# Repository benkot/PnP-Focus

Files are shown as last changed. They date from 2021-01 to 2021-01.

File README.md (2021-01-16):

This is a fork of the PnP-Focus project started by Anat available here:

https://github.com/aruangra/PnP-Focus

Since there are significant Changes with this V2.0 version compared to the original project, let's start fresh with the features.

# PnP-Focus Version 2.0

## Objective:
To build a focus controller which takes arduino controller boards and plug-in controller shields to assemble a focus controller with minimal soldering or wiring.

## Two versions of the project:
* Standalone PNP-Focus Controller
* PnP-Focus Stick Controller

## Features:
* Manual control.
* LCD display (Optional)
* Temperature sensor.
* Local manual motor control using automatic increasing speed changes.
* Independent motor speeds for local button focus position and ASCOM commanded position
* Stepper motor output power down after a positional move to prevent motor from heating due to quiescent current.
* Ability to drive Uni-Polar or Bi-Polar stepper motors.
* Full step and half step motor movements.  
* Switching between full step and half step automatically converts the position counter to new step count and correct transition step code.
* Ability to save position and step mode to non-volatile memory and recall on power-up to restore unit to previously used configuration

* Compatible with Moonlite DRO ASCOM driver with the following compatibility features:
    * Full selection and operation of moonlight DRO ASCOM step speeds using 16, 32, 64, 125, 250 steps/second.
    * Temperature sensor for temperature compensation by ASCOM driver.  Temperature sensor moved to pin A2.
    * ASCOM connection locks mode to driver selected Full step or Half step  mode.
    * ASCOM stop or disconnect records stepper position and step mode to non-volatile memory.

* Additional features added when operating in ASCOM connection which are not provided by    Moonlite Technologies DRO driver:
    * Backlash compensation for outward movement to compensate for gravity and to ensure consistent approach to focus position in either direction.
    * ASCOM moves use soft start with speeds increasing at driver speed intervals, up to the selected driver step speed setting.
    * ASCOM move command have reducing speed as target position is approached to to ensure positional accuracy and repeatability.
    * Provides the ability to use high speed focus slews without loss of accuracy or repeatability.
* Compatible with commercially available focus drives using stepper motors
* Works with the popular stepper motors:
    * ABS3008-002  (12V) RoboFocus Stepper Motor
    * LSG35012F76P (12V) Moonlite Telescope Hi-Resolution Stepper Motor
    * 28BYJ-48  (5V and 12V)
    * 17HS13-0404S-PG27 (12V)

## Installation:

The Original Installation upload approach is obsolete and not use with this version.  Requires users to use the Arduino Integrated Development Interface (IDE) program to load the Arduino firmware files.  The use must modify the user configuration header area to match the code to their specific build and then compile and upload the file to the arduino.  All the individual files are available 
https://github.com/benkot/PnP-Focus 

The entire project files are availble in a zip download in the Github folder to make it easier to prepare and install the firmware.

## Documentation:
Project manual describing the necessary hardware, installation, assembly, user controls and operating principles is available in the Github folder

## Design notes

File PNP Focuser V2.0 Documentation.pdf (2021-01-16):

# Plug N Play

# Focus Controllers

V2.0.2

compiled by Todd Benko, 2021

## Table of Contents

## PREFACE

## Disclaimer

This project is released into the public domain as is where is, with no obligation or responsibility accepted on the part of the author, for any mishaps or failures caused by this product or use of this product. Users intending to use this project or code do so at their own risk and usage of product and code is deemed to be acceptance of those risks. The author(s) accept no responsibility to damage caused to any equipment or goods or self by using the ideas, schematics and code associated with this project, or loss of income or all other losses that may be incurred. No warranty is offered or implied.

## Copyright Restrictions

The schematic, firmware and other code and ideas are released into the public domain. Users are free to implement these for their personal use, but may NOT sell projects based on (or derived from) this project for commercial gain without express written permission granted from the author(s).

## Firmware License Restrictions

If you copy or write new code based on the code in these files you must include a link to these files AND you must include references to the author(s) of this code. Firmware is released subject to the following restrictions

© Copyright Orly Andico, 2014
© Copyright Anat Ruangrassamee, 2017
© Copyright Michael Fulbright, 2018
© Copyright Todd Benko, 2020

Permission is hereby granted, free of charge, to any person obtaining a copy of this software and associated documentation files (the "Software"), the rights to use, copy, modify, merge, publish, distribute, sublicense copies of the Software (from the authors), subject to the following conditions:

1. The above copyright notice shall be included in all copies or substantial portions of this Software.
2. The software may NOT be sold or charged for in any way, either as part of a package, license fee, annual charges or premiums and shall include the copyright notice above.
3. The source-code to any software MUST be made available in full source-code form (including modified source files) and free to download without payment and include the copyright notice above

THE SOFTWARE IS PROVIDED "AS IS", WITHOUT WARRANTY OF ANY KIND, EXPRESS OR IMPLIED, INCLUDING BUT NOT LIMITED TO THE WARRANTIES OF MERCHANTABILITY, FITNESS FOR A PARTICULAR PURPOSE AND NONINFRINGEMENT. IN NO EVENT SHALL THE AUTHORS OR COPYRIGHT HOLDERS BE LIABLE FOR ANY CLAIM, DAMAGES OR OTHER LIABILITY, WHETHER IN AN ACTION OF CONTRACT, TORT OR OTHERWISE, ARISING FROM, OUT OF OR IN CONNECTION WITH THE SOFTWARE OR THE USE OR OTHER DEALINGS IN THE SOFTWARE.

## INTRODUCTION

## Overview

An Arduino-based focus controller named "PNP-Focus". As the name implies, it is to be as easy as "Plug and Play" with little or no soldering. No hassle with firmware upload.
You simply 1) buy the readily available components, 2) stack them, and 3) upload the firmware. The PNP-Focus is just the controller. You still need to mount a stepper motor on your telescope connected to this controller. With motorized focuser you get the higher resolution since a stepper motor may have 2000-6000 steps per revolution. The higher resolution is crucial for imaging. You have the option to control the focuser locally or remotely from the Personal computer (PC). When you do imaging, you control your devices via a PC and software. PC based then leads to automated focusing.

## Features in V2

- Manual control.
- LCD display (Optional)
- Temperature sensor.
- Local manual motor control using automatic increasing speed changes.
- Independent motor speeds for local button focus position and ASCOM commanded position
- Stepper motor output power down after a positional move to prevent motor from heating due to quiescent current.
- Ability to drive Uni-Polar or Bi-Polar stepper motors.
- Full step and half step motor movements.
- Switching between full step and half step automatically converts the position counter to new step count and correct transition step code.
- Ability to save position and step mode to non-volatile memory and recall on power-up to restore unit to previously used configuration
- Compatible with Moonlite DRO ASCOM driver with the following compatibility features:
- Full selection and operation of moonlight DRO ASCOM step speeds using 16, 32, 64, 125, 250 steps/second.
- Temperature sensor for temperature compensation by ASCOM driver. Temperature sensor moved to pin A2.
- ASCOM connection locks mode to driver selected Full step or Half step mode.
- ASCOM stop or disconnect records stepper position and step mode to non-volatile memory.
- Additional features added when operating in ASCOM connection which are not provided by Moonlite Technologies DRO driver:
- Backlash compensation for outward movement to compensate for gravity and to ensure consistent approach to focus position in either direction.

- ASCOM moves use soft start with speeds increasing up to the selected driver step speed setting.
- ASCOM move command have reducing speed as target position is approached to to ensure positional accuracy and repeatability.
- Compatible with commercially available focus drives using stepper motors
- Works with the popular stepper motors:
- ABS3008-002 (12V) RoboFocus Stepper Motor
- LSG35012F76P (12V) Moonlite Telescope Hi-Resolution Stepper Motor
- 28BYJ-48 (5V and 12V)
- 17HS13-0404S-PG27 (12V)

Exceptions
- PNP-Focus units will not drive DC or AC servo motors used in some focuser drive systems.

Caveat
The goal behind PNP-Focus was to use off the shelf components, plug them together without the need to perform any soldering. The primary components can be assembled within the design scope. The real issue could be the components you select to assemble your project may indeed require some assembly or soldering activities. Many of the components from suppliers may in fact not have the header wires installed. Also depending on your housing your interface connections may requires some assembly or soldering. Interface components such as power wires, motor connectors may require soldering assembly depending on components that you source.

## Hardware Variations

There exist two design hardware versions. Both version offer computer focus control through the Moonlight DRO Ascom driver. There is the full size

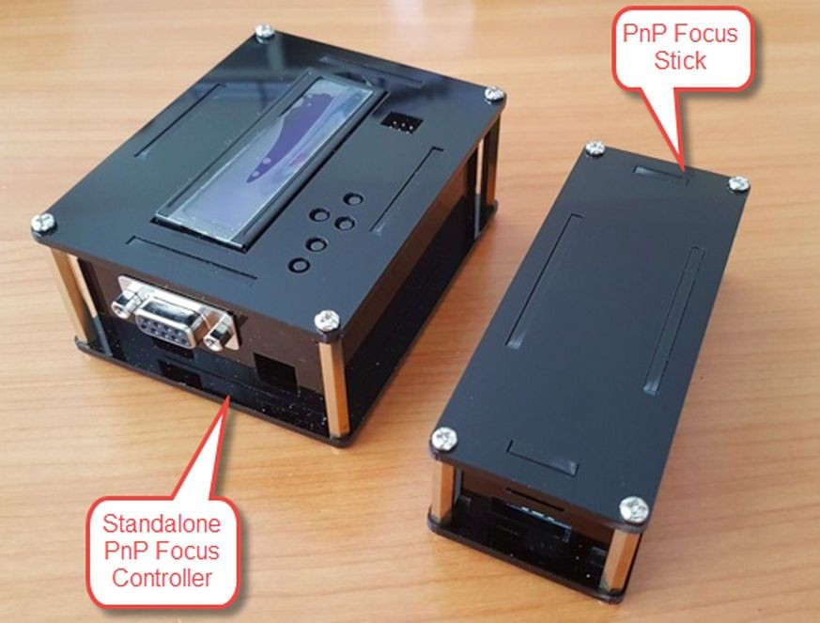
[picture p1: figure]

standalone PNP-Focus Controller offers USB and local button focus control. The PNP-Focus Stick only provides computer focus control via the USB port.

Standalone PNP-Focus Controller
The Standalone focus controller is intended to provide a user with direct control of the focus motor without any need for software or computer. The designed is based on the Arduino Leonardo board, using a plug in LCD1602 display shield as the user interface. The display shield offers a 2 line x 16 character display for status information. The shield includes 6 tactile buttons to provide manual focuser control without any computer connection. Telescopes with an electronic focuser can be used without the need to connect to any computers nor the need to remove the focus motor for simple astronomy usage.
The standalone focus control still provides full computer control when connected using the arduino USB connection and the moonlite DRO ASCOM driver. The same design can run headless, without the LCD1602 display shield installed. The variation would provide using only computer control in the similar form factor.

Required Components

1) Arduino Leonardo ATMega32U4 Controller
The Leonardo board with the ATMega32U4 chip is the board that was used for this build. Technically the pin layout for the Arduino and the Ardumoto board would line up for use with other Arduino controller boards. For simplicity sake just use the Arduiono Leonardo. The code may work with other Arduino board with the same footprint because you use the Arduino integrated development environment (IDE) program to load the firmware. We leave that choice up to those who want to play rather than just using what was chosen for the PNP focus platform.
search “Arduino Leonardo” on by Arduino or keyestudio on Ebay, Amazon or Aliexpress Keyestudio Leonardo, (https://www.aliexpress.com/store/product/Free-shipping-leonardo-R3-development-board-USB-Cable-compatible-for-arduino/1452162_32310214921.html) Ebay, (https://www.ebay.com/b/arduino-leonardo/bn_7024816151)
2) Ardumoto L298P Motor Drive Board
Ardumoto L298P motor drive board can be purchased with different pin assignments The standard for this programs uses

D3 -A motor PWM drive
D11-B motor PWM Drive
D12-A Dir
D13-B Dir
The L298P board is capable of driving up to 2A current per motor connection.
To make things easy just ensure the board you purchase uses Pin 3, 11, 12, 13

for driving the motor. Fortunately, most of them are. Also ensure the socket with leads come with kit so stacking above and below board is available. Search “ardumoto L298P on Ebay, Amazon or AliExpress. Do not confuse this with Ardumoto version 2.3 boards using L293D chips. Their control is totally different and not compatible.

Many of the ardumoto boards come with surface mount pad instead of jumper
pins to select the logic voltage between 5Volts and 3.3Volts. The Leonardo
requires using 5 Volt logic to be selected. Ensure that you place a solder

bridge on the 5V selection pads to set the correct logic voltage. A small single
strand of wire helps to make this bridge. Make sure there is no connection to the
3.3V pad. If it is not selected, move commands will just cause the stepper to vibrate or move really slowly when issuing a move command. This issue was most people’s problem in building their PNP-Focus controller.

Keyestudio Ardumoto Shield (https://www.aliexpress.com/store/product/Free-shipping-L298p-Motor-shield-motor-drive-for-arduino/1452162_2043390148.html) , Ebay (https://www.ebay.ca/sch/i.html?_from=R40&_trksid=p2380057.m570.l1313&_nkw=ardumoto+shield&_sacat=0)

3) 1602 LCD and Keypad Shield
Search “1602 LCD and keypad shield” on DFRobot, Ebay, Amazon. There are various 1602 keyboard shields available and most should work. LCD shield for this project uses Pins D4-D10 and A0. The differences are usually button sizes, additional interface pin and how the LCD
contrast is adjusted.
1602 Shield for this project uses the following pin assignments
D4-LCD D4
D5-LCD D5
D6-LCD D6
D7-LCD D7
D8-LCD Reset
D9-LCD Enable
D10-LCD BackLight brightness adjustment
A0 – is button decoding.

Button readings have two different analog ranges depending on which version is purchased. Need to select using comments // which pin assignment works for your LCD shield in read_LCD_buttons() function.

Make sure the one you select works for the case you plan to use and how you plan to implement the temperature sensor. The DFRobot has longer tactile button caps and has pins to make temperature sensor connection to the LCD shield through the top of the case using solderless pin connections. Others have lower tacktile buttons and there is no need for any pins on top surface so you want pins on the bottom for stacking onto the ardumoto shield. If you do not want to make a different temperature connection through the LCD top surface, use the breakout area of the ardumoto to wire in your temperature sensor connections using soldered wire connections. You could use an internal temperature sensor, an external one through the motor drive cable or a seperate standalone plugin that uses a headphone jack connection which could disconnect an internal temperature sensor connection.

Keyestudion LCD1602 Shield (https://www.aliexpress.com/store/product/1602LCD-Keypad-Shield-For-Arduino-LCD-Display-ATMEGA328-ATMEGA2560-For-Raspberry-Pi-UNO-Blue-Screen-Blacklight/145216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) , Amazon (https://www.amazon.ca/Keypad-Shield-Backlight-arduino-Robot/dp/B07F7GCZNV?s=electronics) , Ebay, (https://www.ebay.ca/sch/i.html?_nkw=Lcd%201602%20Keypad%20Shield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) AliExpress (https://www.aliexpress.com/premium/keypad-shield-lcd1602.html?d=y)

4) DS18B20 Temperature Sensor and Interface
There are so many different ways to connect the DS18B20 temperature Sensor. For the PNP-Focus the sensor data pin will connect to the Analog A2 Arduino pin. The original PNP-Focus used pin A2, however the PNP-Focus stick has a conflict with nano-motorshield. Therefore this version
and firmware code is looking for temperature probe data on Analog pin A2.

The interface requires that the data pin be pulled up to 5V with a pull up resistor either by a non-soldered interface board or by your own wiring application. It basically
depends on your assembly comfort level. The temperature sensor is only

used for temperature compensation focus position moves. The temperature
must reflect the temperature change of your telescope and it will vary unit design variances. There are assembled boards which have resistor and indicator diodes already installed that might be able to placed on outside of housing and just require running wires to the Arduino pins.
Another approach would use a waterproof external temperature probe which would be attached to the shell of the telescope to measure the temperature changes. Another approach might be to install the temperature sensor or module board in the dB9 connector which attaches to the focuser motor. All approaches
may have their differences and any application of temperature compensation is
based on an observed response based on either temperature sensor location.

Using either method you need to observe the focus changes which occur with your telescope prior to applying a temperature compensate rate.
The moonlite focuser lists commands as though temperature compensation would be applied by the focus controller. Moonlight Telescopes Ltd has been determined that temperature compensation is better managed by the ascom driver, rather than the hardware
interface. It has been validated that the temperature
compensation commands listed in the hardware command
interface are not issued by the driver when temperature

compensation is selected. As a result temperature compensation is not enabled when operating the as a standalone controller. The fact that manual focus control is more important to adapt to different users in visual astronomy or other standalone astronomy usage rather than the benefits offered by temperature compensation.

Keyestudio DS18B20 (https://www.aliexpress.com/item/32884815508.html?spm=2114.12010612.8148356.3.6e6f1aeeuFA1dI) , Amazon (https://www.amazon.ca/Waterproof-Temperature-Stainless-Plugable-Terminal/dp/B07LFJR3J7) , AliExpress (https://www.aliexpress.com/item/1834551892.html?src=google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) , Voltateck (https://voltatek.ca/sensors/145-temperature-sensor-ds18b20-module-board.html)

5) Interface Components
You need a variety of interface components to power and connect your PnP Standalone Focus Controller to your focus motor assembly.

Vin Power connection:
12V power cable to power the Arduino and Stepper motor. The ardumoto shield will not drive the stepper motor with only USB power applied. The ardumoto shield requires that Vin
power be supplied at the voltage required to drive the stepper motor. Typically recommend
using 12V stepper motor. The Vin can be connected using the barrel connection of the
Leonardo or the terminal strip on the ardumoto. For the PNP-Focus Stick it must be connected to the terminal strip. Solderless barrel connectors are available from various sources.
Amazon (https://www.amazon.ca/VCE-Pairs-2-1x5-5mm-Adapter-Camera/dp/B078X47M5H) , Adafruit (https://www.adafruit.com/product/368) , Ebay (https://www.ebay.ca/sch/i.html?_nkw=Barrel%20To%20Screw%20Terminal%20Connector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)
- USB micro cable to program the arduino and to drive unit with PC using
ASCOM driver. The assembly of the PNP-Focus does not provide good accessibilty to the USB interface. One solution is to use a USB patch cord with a panel mount usb connector. This way you do not need a specific as built case to house the PNP-Focus controller. To conserve space, recommend looking for
the 90 right or left usb patch cords.
AliExpress (https://www.aliexpress.com/item/32805000569.html)
- A cable interface from the controller to the motor. Many focus motors use a dB9 connection. A dB9 male-female cable would be used if a dB9 connector was installed on the controller housing
- option using an Ethernet cable and installing a female Ethernet jack on the controller housing and then a RJ45-dB9 adapter at the motor drive connection.

Standalone Computer Only Configuration Option
If you like standalone hardware and case you plan to use and only want to drive it from a computer ASCOM driver, you can just omit the installation of the LCD1602 display and keyboard shield to produce only computer access focus control. For this configuration, you need to adjust the user configuration in the arduino firmware code to comment out LCD1602 display and keyboard shield as it is not installed.

Case and Housing Options
Standalone PNP-Focus Controller builders have found various methods to enclose their controller boards. Anat used flat laser cut plexiglass material to create a jointed box which is fastened together with 4 screws. The laser cut dxf files are included in the zipped file assembly.

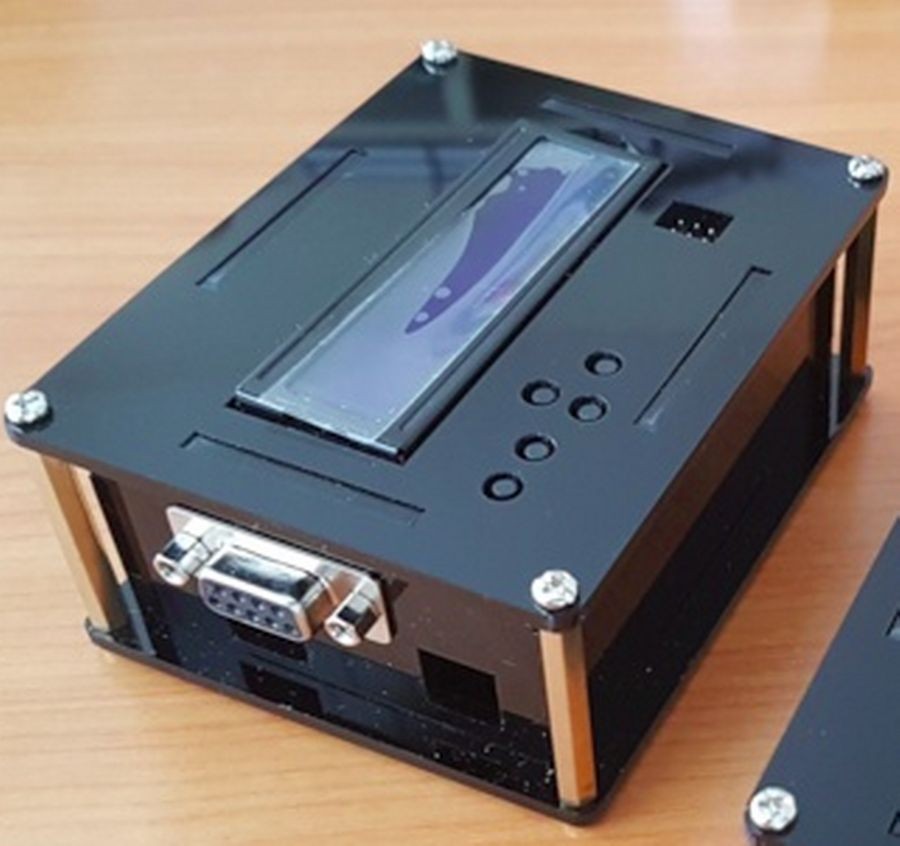
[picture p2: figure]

Mr. Tom K. created a 3D printed case and lid to enclose his standalone PNP-Focus controller.

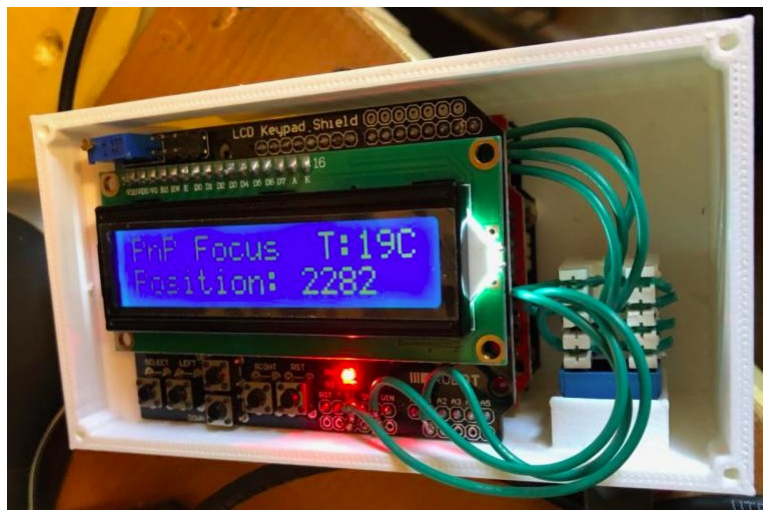
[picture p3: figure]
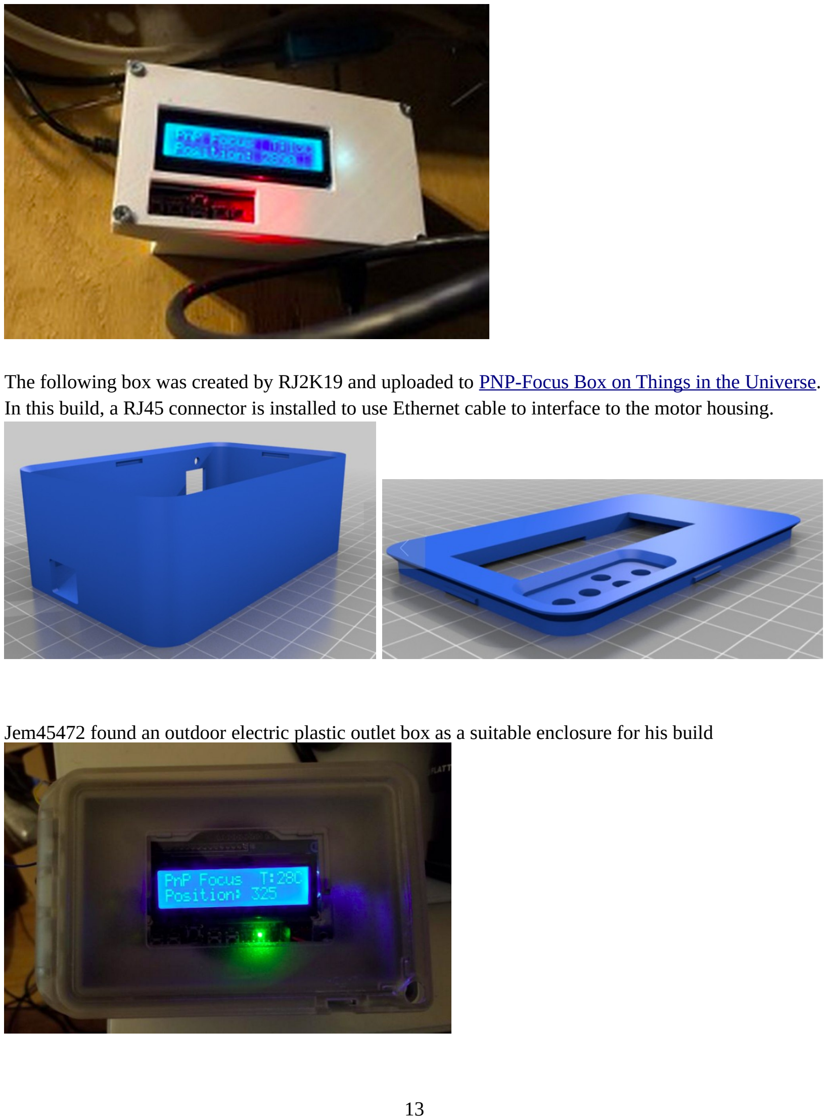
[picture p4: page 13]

The following box was created by RJ2K19 and uploaded to PNP-Focus Box on Things in the Universe. (https://www.thingiverse.com/thing:4075523) In this build, a RJ45 connector is installed to use Ethernet cable to interface to the motor housing.

Jem45472 found an outdoor electric plastic outlet box as a suitable enclosure for his build

I used a standard plastic Hammond case 120mm x 65mm x 40mm and just carved out the holes and slots for the interface components.

Assembly Notes:
1. Many of the Arduino and shields do not come assembled with the stacking pins installed. The ardumoto board is in the middle of the stack so it must have stack-able headers installed.

When you stack the boards together, you want to ensure pins are aligned such that all digital and Analog I/O pins align on each stacked board.

2. Wiring the stepper motor is a bit confusing. It doesn’t help when board silkscreen numbers or user documentation doesn’t match with assembled components. For instance Moonlite hi-res focuser is documented as the following pin and wire colour assignment.

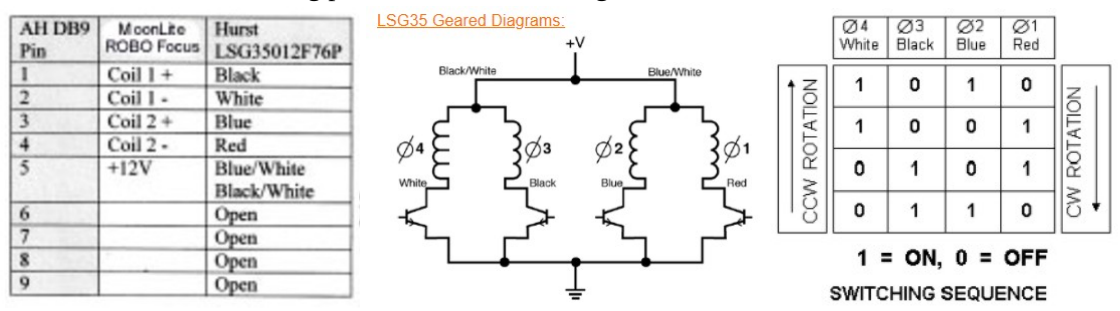
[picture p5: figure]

However, disassembly of a Moonlite hi-res focus motor on a Newt telescope found Blue on the dB9-pin 1, Red on pin 2, Black on pin 3 and white on pin 4 and the blue/White/ Black/White wires both connected to pin 5. This is a significant difference and if we plot out true table in firing the same order but in a different wire order we find the following:

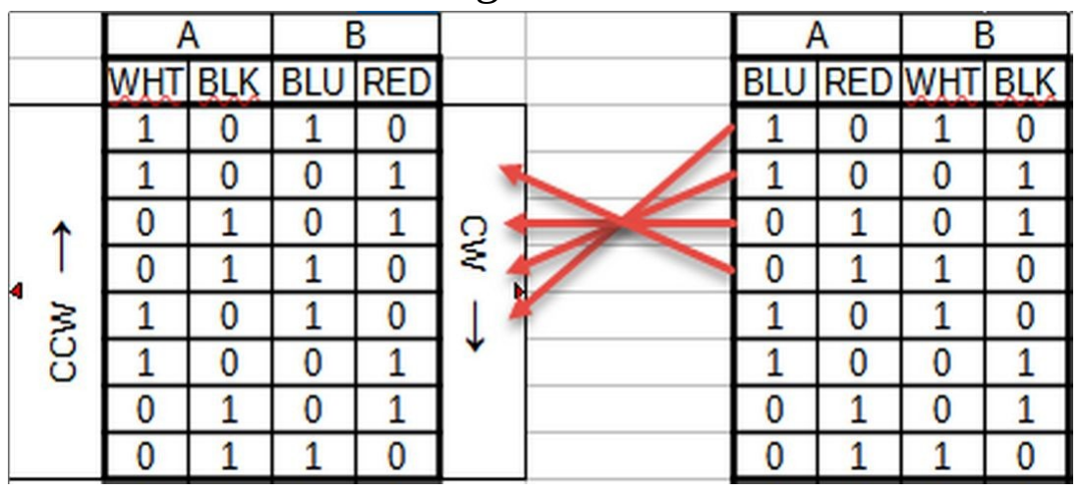
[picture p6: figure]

The left side is the documented order and the right is same order firing but wired in reverse. If we look for the same exact logic sequence of the right table in the left, we find the firing order produces an opposite rotational direction.

This is significant to your installation of
the stepper motor to the telescope. The
focus controller is designed where

increasing the step count produces an outward focus movement. If you find that your motor is running inward with increasing motor steps, all you need to do is swap the wires in pair A and B output on the Motor shield or on your stepper motor connector. Voila, the focus runs in the correct direction. More details about the specific wiring connection are provided later in the Operating Principals section.

## PNP-Focus Stick Controller

The desire to have a smaller focus controller which can only be controlled by computer appeals to many users. With computer access control, there is no need for the display and keyboard shield. You could simply not install the LCD1602 shield and use the stand alone board configuration. However there is a smaller Arduino unit which can make a smaller focus controller unit. The PNP-Focus Stick uses an Arduino MICRO board with a nano motor shield which fits the smaller pin layout configuration.

Components required:

1) Arduino Micro ATmega32u4 Controller:
Ensure you select the Arduino Micro ATmega32u4 5V 16MHZ

100% for Arduino Micro Replace pro mini and not the Mini or Mini Pro versions as those have a different pin footprint which does not match the motor shield. When assembling this board you need to ensure the pins are installed pointing downwards so it will plug into the and above the NANO motor shield.
Ebay, (https://www.ebay.ca/itm/New-Arduino-Micro-ATmega32u4-5V-16MHZ-100-for-Arduino-Mirco-Replace-pro-mini/331809999256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)
2) NANO Motor Shield:
Nano motor shield board is believed to be standardized with the same pin assignments used in the program. When searching, just confirm the following pin assignments.
The standard for this programs uses
D3 -A motor PWM drive
D11-B motor PWM Drive
D12-A Dir
D13-B Dir
To make things easy just ensure the board you purchase uses Pin 3, 11, 12, 13 for driving the motor.
The shield can supply 2 amperes per channel, for a total of 4 amperes
maximum.
Input and Output

This shield has two separate channels, called A and B, that each use 4 of the For Arduino pins to drive or sense the motor. In total there are 8 pins in use on this shield. You can use each channel separately to drive two DC motors or combine them to drive one Bi-Polar stepper motor. PNP-Focus only uses the code to drive the stepper motor operation and not the DC motor operation. The shield's pins, divided by channel are shown in the table below:
Function | pins per Ch. A pins per Ch. B
Direction | D12 | D13
PWM | D3 | D11
Brake | D9 | D8
Current Sensing A0 | A1

AliExpress (https://www.aliexpress.com/item/32799216665.html) , Amazon (https://www.amazon.ca/Nano-L298P-Channel-H-Bridge-Stepper-Driving/dp/B07KFBNSTD) , EBay (https://www.ebay.ca/sch/i.html?_from=R40&_trksid=p2380057.m570.l1313&_nkw=nano+motor+shield&_sacat=0)
3) Temperature: Can use the same resources as the PNP-Focus stanalone version. Soldering or wirewrap required to pins into place for proper temperature placement. For the temperature you need the same connections as in the standalone version to +5V, Ground (GND) and the centre data pin connected to Analog 2 (A2) pin. It is conceivable that the PNP-Focus Stick would be used to build a complete focus assembly with the controller and motor in one housing and attached directly to the telescope. In this situation you really need to ensure the temperature probe gets outside the housing. Both the stepper motor and the Arduino boards will produce heat inside the housing. That heat will throw off your focus set point because it will cause the focus to move after you have each use of the focus drive.

PNP-Focus Stick Assembly
1. Typically the Arduino Micro and the Nano motor shield are delivered without any header pins installed. You will want to install the Micro header pins downwards and you will need to install female header pins on the NANO motor shield. NOTE: Do not install a header pin on Vin pin on the Micro board. See the technical specification at end of the document about why the Vin connection is removed between the Micro board and the Nano Motor Shield for all applications.

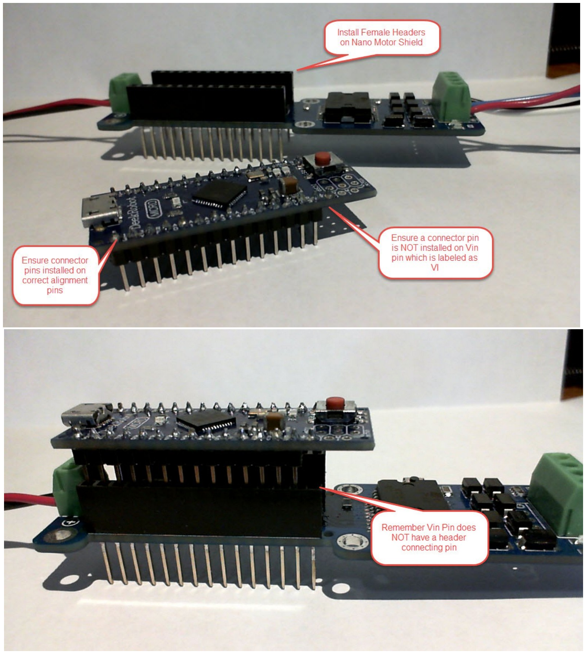
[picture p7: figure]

2. If using a stepper with voltage > 5V then connect a power supply connection to power the Stepper motor with the required voltage.

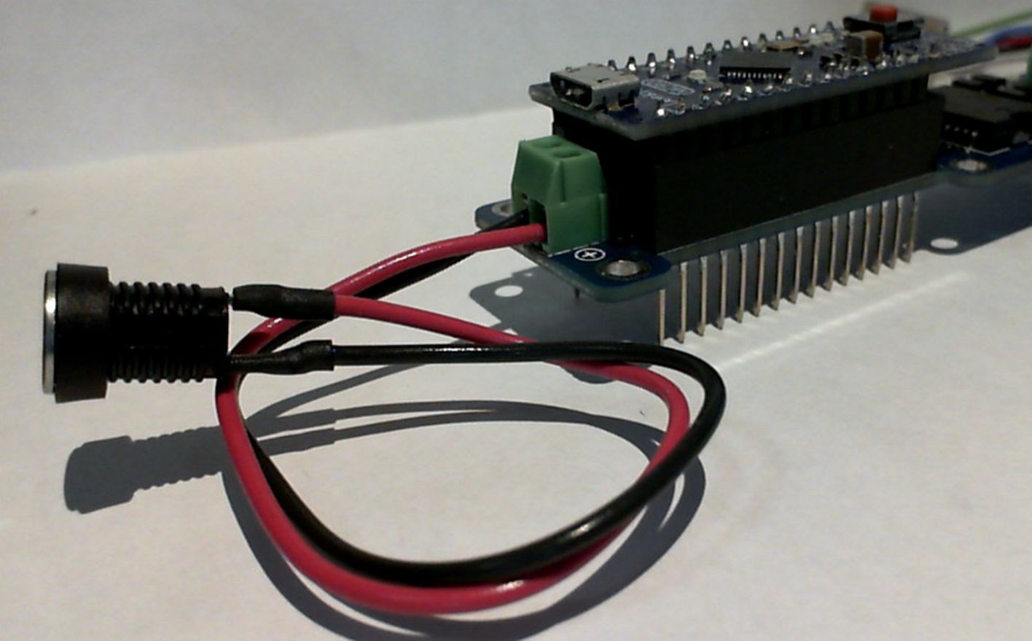
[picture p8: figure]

3. If you are intending to only use a 5V version of 28BYJ-48 Stepper motor then you need to supply a 5V supply to the motor shield board. One approach is the same as previous step where 5V would be supplied from external power cable. A simple approach is to use the 5V power from the USB connection to the MICRO. In this case you need to connect 5V pin to Vin pin on the bottom of the Nano Motor Shield.

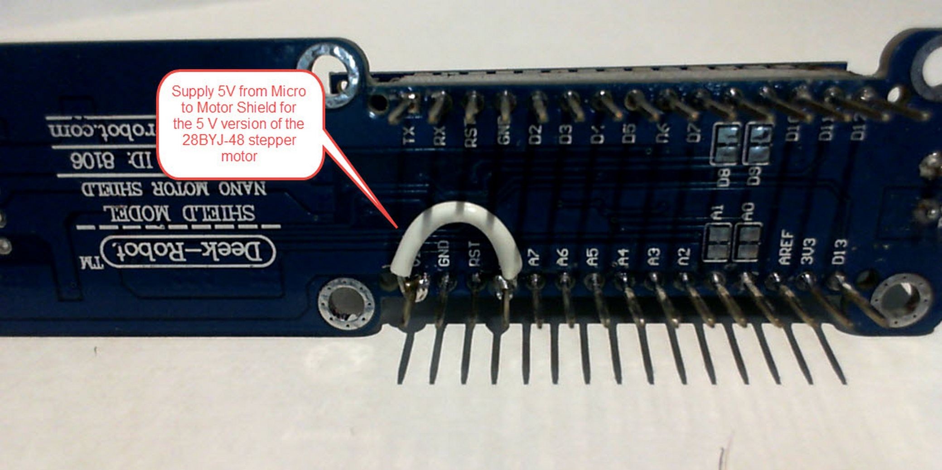
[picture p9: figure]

4. Don’t connect motor yet. Power up the stick with both USB and designated motor power connection and load the specific user configured firmware into the MICRO.
5. Launch a program which can connect to the PNP-Focus Stick with the Ascom Connection. Make sure to select only Full step operation, and for testing purpose set speed to 16 steps/second.

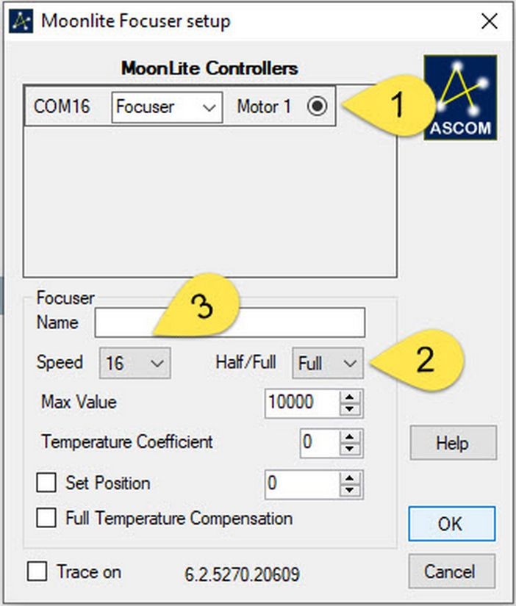
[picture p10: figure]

6. Connect to the focuser and move the focuser to step position 2. Observe the Output Voltage Polarity LED indicators on either side of the motor connection terminal block. In Full Step mode an LED on both A and B output should illuminate for each step. The LED should illuminate during the step move and after 3 seconds extinguish, indicating the power has been turned off to the stepper motor. Full step has a 4 step sequence so go ahead and step one at a time through position sequence 0-1-2-3-4-5-4-3-2-1-0 and observer the sequence should look something like the following.

7. Now power things down and connect up the lead to the stepper motor. Refer to Operating Principles section on Motor Wiring connections.
8. Repeat tests again with motor connected to ensure proper stepping sequence. Once completed you can then use a larger step move to determine if you have the correct stepper motor rotation direction for an increased step position.
9. Temperature Option: Attaching a temperature probe is a bit more challenging if you desire. I chose to go with an internal temperature sensor. I simply bent the lead for pin A2 over at 90 degrees and soldered a simple temperature probe board on to the lead before trimming the lead. I then ran wire

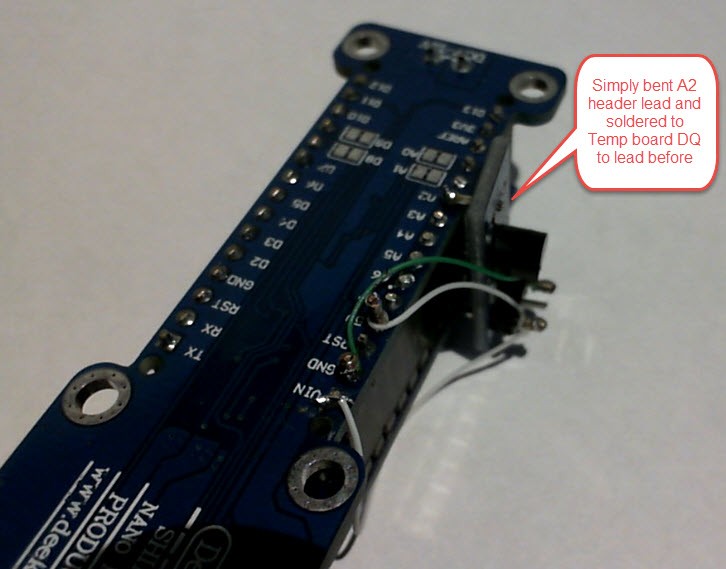
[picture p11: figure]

wrap wire to connect the 5V vcc and Ground connections to the other pins before trimming the leads. Its not a true telescope temperature indication, but it will work for my purpose. Here are picture of a possible installation option:

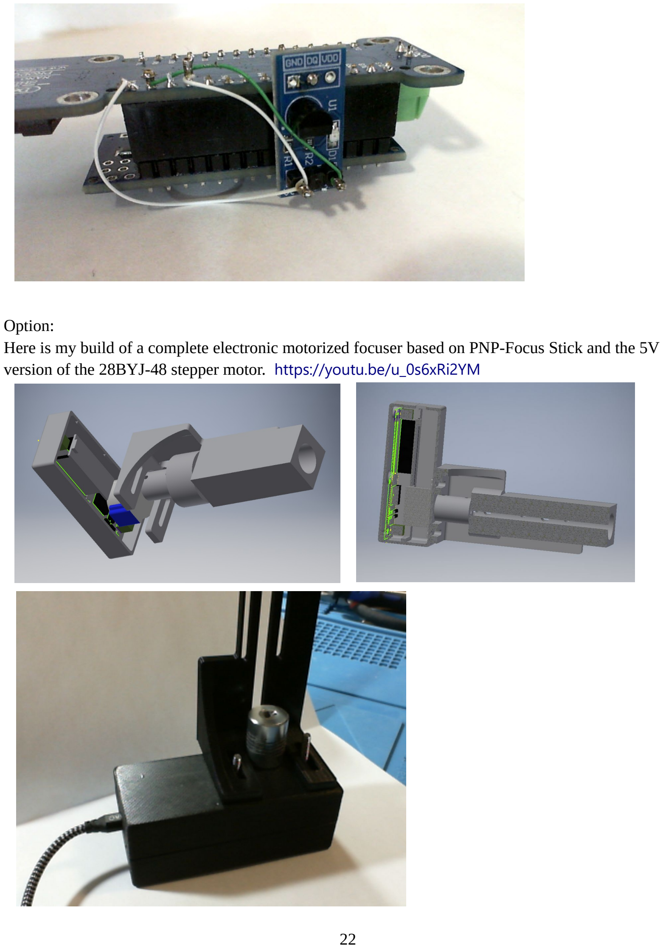
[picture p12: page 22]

Option:
Here is my build of a complete electronic motorized focuser based on PNP-Focus Stick and the 5V version of the 28BYJ-48 stepper motor. https://youtu.be/u_0s6xRi2YM

## Installation

## Firmware Installation

The firmware with this version is user configurable and will work with both the Standalone PNP-Focus controller and the PNP-Focus Stick. The difference is that a user must modify the user definitions at the start of the arduino code to fit their stepper motor configuration and the installation board options.

### 1. Download and install the Arduino Integrated Desktop Editor (IDE) from the location:

You only need to install the program on a computer which will be used to load the firmware into the Arduino board.

2. Download the project files for the Github repository from https://github.com/benkot/PnP-Focus on the same computer as the Arduino IDE. Recommended directory is Documents\Arduino and unzip the files. Descend into the directory for the PnPFocuser-V2.0 There are many different forks of the original version so you need to have the version which identifies PnPFocus-V2.0.
3. Double click on the file: PnPFocus-V2.0.ino to launch the Arduino and open the file in the IDE.
4. The front or top part of the firmware code contains user definitions which must be tailored to your configuration and operational choices.
4.1. Motor operation can be in Full step or Half step mode. Many stepper motors do not appear to operate in a repeatable manner in Half step mode. However if desired to operate in Half Step mode, change the line in the firmware code:
enableHalfStepMode = true; | // false only enables only Full Step operating
mode, true enables both Full step and Half step operating modes.
4.2. Backlash Compensation: Some focus motors when racking out create a shift due to gravity on the weight of the equipment on the focuser or the play in the gearbox between the motor shaft and the output shaft. To compensate for this issue it is often desired to approach the focus position by first overshooting the outward move and then have a consistent inward approach to the target position. The backlash compensation will only apply to ASCOM driver moves. Any position moves less than 5 steps will not have backlash compensation applied to the outward position movement. Inward postion movement never have backlash applied due to the nature of the movement and effects of gravity. If using the Ascom driver temperature compensation features the temperature moves are small one step changes at a time and will not have backlash compensation applied. The DRO ASCOM driver does not have ability to set the backlash value. Therefore backlash value must be set in the user configuration area of the firmware code.
unsigned short backlashValue=0; | // increase this value to indicate how many
steps your focus motor needs to overshoot to compensate for focus backlash. The focus motor will rack out this number of steps extra and then back in the same number of steps to arrive at the target position.

Note: Some image capture software include their own backlash compensation control option in their program operation. If you want to use backlash compensation, ensure you only apply configuration values to either the PNP-Focus firmware or the capture software but NOT both at the same time. If you want to use image capture for backlash compensation, then ensure backlash value above is set to 0 in firmware user options.

4.3. The LCD1602 display Shield Configuration: If you have built the standalone PNP-Focus version you have a choice have the LCD display is installed or not. If you have built the PNP-Focus stick version, the LCD1602 configuration line must be configured as not being installed.
If the LCD1602 display shield is installed following line should be
#define LCD1602Shield

If not installed, the line requires comment characters (//) added so it looks like
//#define LCD1602Shield
4.4. Temperatures Units if using a DS18B20 temperature sensor: The temperature in both the standalone display and the ASCOM driver, values can be either Celsius or Fahrenheit. Change the line in the firmware code to your temperature unit choice.
bool displayFahrenheit = false; | // false = temperatures in Celsius., true =
temperatures in Fahrenheit. If set to true, both display values and temperature compensation must use temperature values in Fahrenheit.
4.5. All standard user configuration is completed. The firmware code will now program either the Standalone PNP-Focus controller or the PNP-Focus Stick hardware configuration.
4.6. If installing the LCD1602, program the unit and validate the tactile switches function properly. Different manufactures of LC1602 boards may use different resister combinations for the switch measured values. You may need to change the commented out lines in the firmware “read_buttons” function if you encounter problems with your button action.
5. Assemble your PNP-Focus controller boards
5.1. Arduino leonardo (bottom), Ardumoto shield (middle), LCD1602 shield(top) {Standalone}
5.2. Arduino leonado (bottom), Ardumoto shield (top) {Standalone headless}
5.3. Micro motor shield, (bottom), Arduino micro (top) {Focus Stick}
6. Connect your computer to the Arduino using a USB cable. The Arduino should self register as a USB comm port.

7. Use the Arduino IDE with the user modifications to compile the firmware code and load the arduino with the following steps:

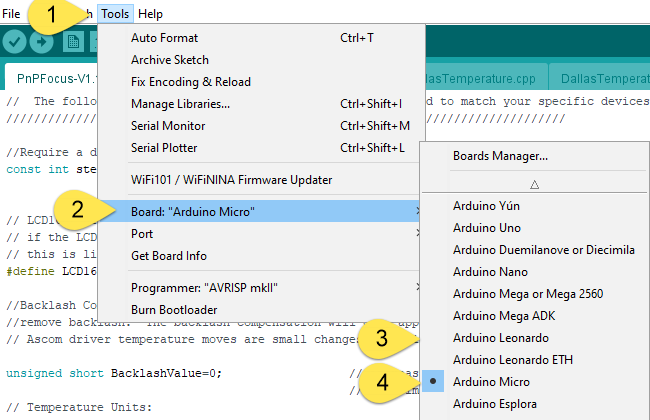
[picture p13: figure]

7.1. Set the board type in the IDE
interface using menus Tools –
Board – Select either the
Arduino Leonardo or Arduino Micro as required for your Arduino board.
7.2. Set the communication port to which your computer is
connected to the Arduino.
Use menus Tools – Ports
Select the appropriate com port which is identified as your Arduino.
7.3. Compile and load the firmware onto the Arduino from the IDE using the
upload button on the tools ribbon.
The bottom IDE status bar will
display “Compiling Sketch”, then “Uploading...” then “Done
uploading” if the process was successful.
7.4. If you have the standalone PNP-Focus with the LCD1602 shield, try the buttons for proper functionality. If buttons respond different than expected, then there is a different set of threshold values to use in the read_buttons function. In the following example, the newer board thresholds are commented out. Add comment blocks to older board section and remove comment block from new board section. Reload firmware and try again.

// For newer boards may use these thresholds /*
if (adc_key_in < 50) return btnRIGHT;
if (adc_key_in < 250) return btnUP;

if (adc_key_in < 450) return btnDOWN; if (adc_key_in < 650) return btnLEFT;
if (adc_key_in < 850) return btnSELECT;
*/
// Older boards or clones may use these threshold:

if (adc_key_in < 50) return btnRIGHT;//increase value if (adc_key_in < 195) return btnUP; //screen ON/OFF if (adc_key_in < 380) return btnDOWN; //No Activity
if (adc_key_in < 555) return btnLEFT; //Decrease value
if (adc_key_in < 790) return btnSELECT; //Stop and save

// use comment block /* */ to comment the whole group which is not applicable to your LCD1602 shield

7.5. Recommend that you save the PnPfocus file with your specific configuration changes. This way it will be ready to use any time in the future for loading additional focus controllers for different telescope configurations.

## User Interface Operations

## Standalone PNP-Focus Button Controller

The PNP-Focus controller with the LCD1602 has 6 buttons for local user control. The buttons are typically labelled on the shield from left
to right as Select, Left, Up, Down, Right and Reset.

Select Button: Save and Stop button. If the focuser is
moving this will abort the move and will also save the current position to non-volatile memory. Typically this is used at the end of an observing session prior to shutdown if the focuser is not racked all the way in. The current position will be saved. The next time the focuser is
powered up it will start with the current position as the
last save value.

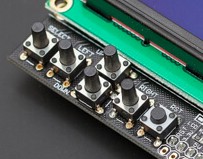
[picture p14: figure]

Left Button: Will decrease the focus motor position count which should rack the focuser inward if the focus motor is installed and wired correctly. Holding the left button will move the focus motor in an increasing speed manner. Movement will start of slowly at 2 steps/second. The speed will increase at 5 second intervals using 10, 50, 100 and 200 steps/second increments. The ramping speed control provides precise small step position response for accurate focus placement, yet still provides easy access to rapid focus position changes.

Right Button: Will increase the focus motor position count which should rack the focuser outward if the focus motor is installed and wired correctly. Holding the Right button will move the focus motor in an increasing speed manner. Movement will start of slowly at 2 steps/second. The speed will increase at 5 second intervals using 10, 50, 100 and 200 steps/second increments. The ramping speed control provides precise small step position response for accurate focus placement, yet still provides easy access to rapid focus position changes.

Up Button: Display brightness control. The display brightness cycles through 5 different brightness levels to enable unit to be totally off for night operation to very bright for daylight operation. Pressing the up button will cycle the brightness through the 5 brightness levels of Off (0), Very Dim(1), Medium brightness (5), bright (20) and Very Bright (200).

Down Button: Changes the stepper mode to either full step or half step mode. When the ASCOM driver is connected and sets the step mode, the down button is locked out from making changes. When step mode is changed the current counter position will change to represent the current value in full steps or half steps.

Reset Button: When pressed will reset the Arduino to a power up state. The Arduino will stop all functions and reload the firmware from memory and restart as if power was just applied.

### Standalone PNP-Focus Status Display

The Standalong PNP-Focus controller with the optional LCD1602 display shield provides a 16 character, 2 line visual status display. The following are display keywords and their meanings.

1. PnPFocus – appears on top line at left edge to identifies the unit name as PnPFocus on powerup.
2. S/R3600 - Appears on top row on right side only during the first Power- up. T to identify the firmware is programmed with the stepper rotation of 3600 steps/revolution. The value is set by the user when programming the unit and needs to match the focus stepper motor for the number of full steps per revolution. The display is provided verification of unit configuration. Useful you have multiple controllers for different stepper motor installations.
3. CP:XXXX - Appears on the bottom row at left edge and reports the Current Position value. The current position range is 0 – 65535 steps. You should measure your focuser travel from complete racked in to complete racked out position to determine you actual focuser movement limits. The current position value will change with each step of the motor given the motor. When the stepper mode is changed from full steps to half steps the current position will half and when changed to half step mode the current position will double the value at the change.

Increasing current position must always represent racking out of the focus position for PNP-Focus to operate correctly.
4. T:20C or T:68F or T:N/A – Appears on the bottom line on the right side to display the current temperature value in Celsius or Fahrenheit if the DS18B20 temperature sensor is installed. The value is the rounded to the nearest integer and is update either every 30 seconds for standalone, or every time the ASCOM driver queries the current temperature. If the DS18B20 sensor is not installed or there is problem communicating with the sensor, the display will indicate Not Available (N/A).

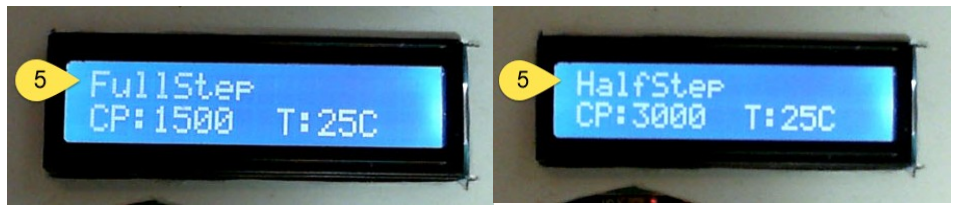
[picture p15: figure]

5. FullStep or HalfStep – appears on the top row when the down button is pressed and indicates the stepper move operation has changed to either full step mode or half step mode. When the stepper mode is changed from full steps to half steps the current position will double and when changed to half step mode the current position will half the value at the change so the current position will report the equivalent number of steps.

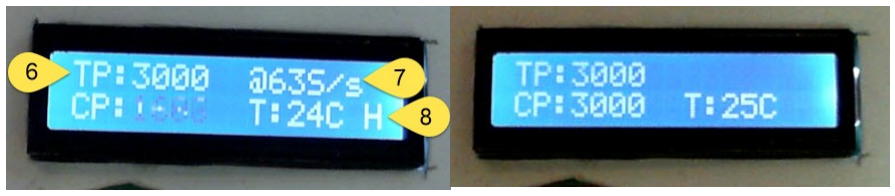
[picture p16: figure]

6. TP:XXXX – Appears on the top row at the left edge and reports the Target Position value. The Target position will be displayed any time the ASCOM drive issues a move to a specific position. The value will also display the current target position if temperature compensation is enabled and moved the focus position off of the last moved position. The Target Position value is used to manage all ASCOM driver position changes. Temperature compensation will change the TP value in the PNP-Focus to move the motor but will remain fixed the the last moved value in the ASCOM display. When a backlash value is entered in the user firmware settings, the target value remains fixed, but the current position will overshoot the target position, pause and then return back to the target position. A rack in position change will move direct to the target position. This ensures the target position is always approached from the same movement direction. When the ASCOM driver is disconnected the TP display will return to PNP-Focus to indicate system returned to full standalone operation.
7. @XS/s – Appears on the top row on the right side when the left or right buttons when a motor movement is requested or when a target move is commanded by the ASCOM driver. X displays the motor speed in Steps/second. The value displayed is always the current motor speed in

Steps per second. The speed dynamically change with left and Right button press holds for manual movements. The values also change with a ASCOM commanded move to manage a soft start and an approach to the target position. The motor speed value will disappear within 1 second of the motor stopping
8. H or F – Appears on the bottom line at the last right character. When present, the H indicates the Ardumoto drive output stage is active in Half Step mode and power is applied to the motor. When present, the F indicates the Ardumoto drive output stage is active in Full Step mode and power is applied to the motor. When the commanded moves are compete, the drive will remain active for 3 seconds before being disabled.
9. Stopped and Saved – Appears on the top row when the select button is pressed to perform stop and save position function. The current position and the step mode values are written to non-volatile memory and will be restored on next power up.

## Moonlite DRO ASCOM Controls

ASCOM DRO 6.0 Driver Download: Moonlite DRO Setup.zip (https://focuser.com/media/Downloads/MoonLite_Software/Ascom/MoonLite%20DRO%20Setup.zip)
Reference Material: Hi Res Stepper Motor 2015.docx (https://focuser.com/media/Downloads/MoonLite_Software/High%20Res%20Stepper%20Motor%20Combo%202015.docx)

The PNP-Focus is configured to accept and respond to commands issued by the Moonlite Telescopes Ltd. DRO ASCOM focus driver. The DRO driver is backward compatible to many of the moonlite focus controller product. As such there has been some issues connecting the PNP-Focus to the DRO driver. When the new version was released, the DRO driver would not recognize the PNP-Focus original firmware. The responses to serial interrogation by the driver appeared to be part of the problem. The DRO driver has some method of determining if the controller is a single or dual motor controller. Originally it appeared that the response to second controller requests and response to version was the reason for the issue. Testing was compared using an existing original moonlite mini focus controller. If the mini controller was ever connected to the computer the DRO focuser responded with single focus control configuration. If it was never connected to the testing computer, then the DRO responded with a dual controller configuration. The Moonlite Telescope single controller responded with version 13 and the documentation suggests the dual controller will respond with version 23. Even with trying these values in the firmware version, there was no consistent determination on how to invoke single controller configuration. The DRO interrogates all the serial ports and only displays ports which respond correctly upon initial setup interrogation.

DRO ASCOM Focus Driver Setup:
ComPort: After interrogating all the available ports only the focuser devices will appear in the list. You must select it to be used as a focuser and the click the button to make it active.

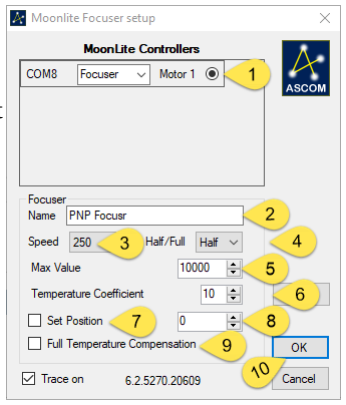
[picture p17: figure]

1. Name: Enter a name which defines this focus device. It might be primary telescope.
2. Speed: Select a speed value for the maximum speed for which PNP-Focus will drive. The values are 16, 32, 64, 125 and 250 steps / second. Because PNP-Focus uses a soft start and soft approach to target position, the value can be selected to a relatively high value. Often heavy focus tube loads can lead to focus tube slip if the speed is too high for extremely heavy
loads. Determine the best value for equipment load and
focuser configuration.
3. Half / Full: Sets the stepper operation mode when the focuser connection is established.
4. Maximum Value: Enter the value which is determined to be the maximum value which can be entered in the target position field. Usually the value will be the number of full steps or half steps which moves the focuser from fully racked in to racked out.
5. Temperature Coefficient: Enter a value which represents the amount of focus position change for the telescope and is expressed in steps per degrees. If the PNP-Focuser is set to display Celsius or Fahrenheit, the same unit is used for the coefficient. The value entered can be either positive or negative. Positive value results in increase position changes with increases in temperature changes. Record a number of focus changes with value set zero and reported temperature over the course of several nights to determine your telescope temperature coefficient.
6. Set Position Enable: The check box will enable the focus position to be set to the value in the position field when the PNP-Focus controller is connected. The set position will only apply once and then cleared once the command is passed to the controller.
7. Position Field: Enter the value for which the set position will assign the controller as the current position when making the connection to the PNP-Focus controller.
8. Full Temperature Compensation: When enabled all current positions are calculated as the corrected current position with the temperature coefficient. The value displayed in the ASCOM current position will not agree with the PNP-Focus position because the temperature coefficient has been applied to the value sent to the PNP-Focus controller. Also the Target position sent to the PNP-Focus will not match the values reported in the PNP-Focus display. Unlike the name suggests, a temperature change will report a target position change in the ASCOM target position but will NOT actually move the focus motor. The value represents the current equivalent focus position based on the temperature change. Using full temperature compensation will only move the focus to the calculated position and will not make any focus change for any further temperature change until the next position move. HIGHLY RECOMMEND to leave this option DISABLED unless you fully test the effect with your system. It may not make sense and may NOT drive your telescope focus position the way you want.
If using the full temperature compensation you need to ensure your focus v-curves have been performed with full temperature compensation enabled during the focus curve recording. The focus will be moved to a position representative of the temperature change offset. Secondly the focus will not move after the target position move. The ASCOM current position value will now provide how much the focus position has shifted since the original target move. It can be used to indicate how much you are now out of focus, and provide some insight when to invoke the next focus routine. There are telescope operations where it makes sense to enable full temperature compensation. Test and confirm before use.
9. OK: When all the settings are set press OK to accept the settings and will be applied when the PNP-Focus controller is connected.

When the focus is connected, the ASCOM controlled program will have controls which allow you direct control of the focus motor and position. Every program has their own unique controls to implement the focus controls. The following example is how NINA employs the DRO focus driver controls. Other programs may be have different labels but the functions should be the same.

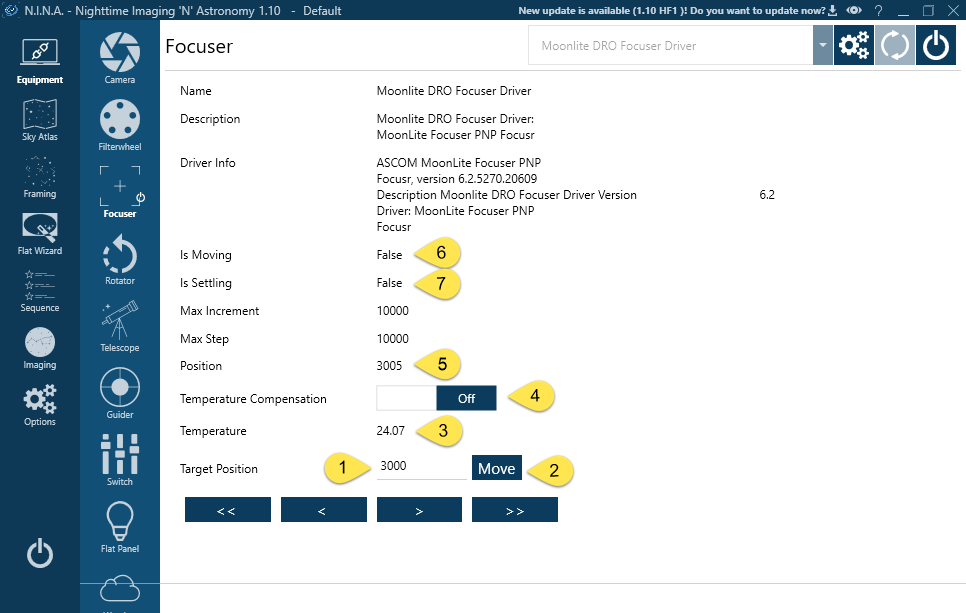
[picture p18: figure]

1. Target Position: Enter the step position you desire the focus motor to be driven. The target command will not be sent to the PNP-Focus until the move button is pressed. The value entered is litterally the count of steps depending on the stepper mode in half or full steps. The ASCOM program may not indicate the current stepper operating mode.
2. Move Button: When the button is pressed the value in the target position field is sent to the PNP-Focuser and executed as a move.
3. Temperature Value: The DRO focus driver interogates the PNP-Focus every 5 seconds and produces a running average for which temperature compensation calculations will be based. Remember this temperature may not fully represent a real air temperature. The temperature is based on where the temperature probe is located and the latency effects.
4. Temperature compensation Enable ON-OFF control. In this example temperature compensation is already enabled. With full temperature compensation disabled in this example, the current temperature compensation gets zeroed with every target position move. Any temperature change after the move will indicate a focus position change based on the temperature coefficient.
5. Current Position: Displays the current focus position. When a target position is set and move is executed the PNP-Focus will drive the focus to the target position and report the position. When temperature compensation is enabled and full temperature compensation is disabled, the current position is the value will change with temperature, the target position will not change however the current focus position will and the motor will move the focus tube to the current focus position. Thereby focus will move. This may be good or bad depending on your focus tube position bearings. If imaging it may however produce a position change if you have a bad focus tube. Temperature compensation can be a delight or a nemisis to Astroimaging depending on the equipment. Temperature compensations position changes occur very slowly and are not subject to backlash compensation actions.
6. Is Moving: Indicates focuser is moving based on a target position move command.
7. Is Settling: Is not provided by the DRO ASCOM focus driver. Therefore when PNP-Focus slows to approach the target, the Is Settling value is never reported.

## Operation Principles

## Choosing Stepper Motors

Motor Wire Configuration
Basically all stepper motors are DC armature motors with two coils which are 90 degrees apart from each other to provide the ability to step or cog the motor shaft by the step coil. The two most common motor configurations are Uni-Polar or Bi-Polar.

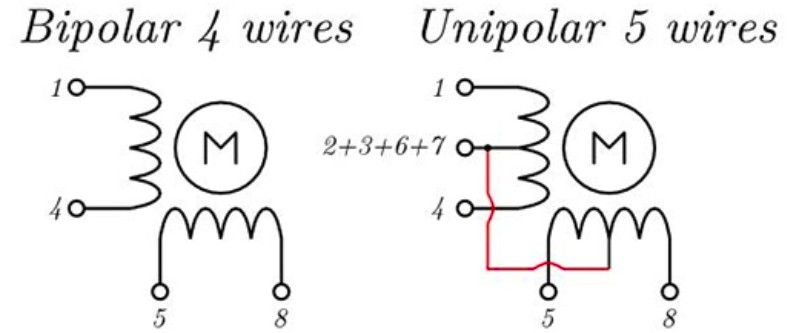
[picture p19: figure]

Bi-Polar motors only have two leads for each stepper coil. Voltage applied across the coil causes current to flow through the coil, inducing an electro-motive force which pulls the motor shaft to a position. In order to create the position step, the voltage must swap between the leads between alternating steps for the coil. For a 12V stepper in one step pin 1 is 12V and pin 4 is ground or 12V return. For the next step change for that coil the applied voltage must swap so Pin 4 is 12V and Pin 1 is ground or 12V return. Hence is why it is called Bi-Polar because each coil has two operating voltage polarizations.
Therefore the stepping sequence might look like
1 | 4 | 5 | 8
GND | 12V GND 12V
GND | 12V | 12V GND
12V | GND 12V GND
12V | GND GND 12V

The Uni-Polar motor can come in a variety of wiring configurations. Uni-Polar motors only have one polarization where positive voltage is applied only to one lead per coil. If the motor is 5 wires then each coil has a centre tap and the two centre taps are tied together for the 5th wire lead. If it is a 6 wire, then each coil is centre tapped and each one coil centre tap is 5th lead and other centre tap is the 6th wire lead. Highly unusual but it could also come as a 8 wire stepper motor. In this situation each coil is actually made up of two coils of which each has a separate top and bottom lead. It then becomes very difficult to identify which lead is for which coil and which is the top and bottom of the coil to form the centre tap lead. Uni-polar motors are typically driven by a single voltage source and the voltage polarity never changes. Typically the center tap would have 12V or Vcc and then you just connect one of the leads to ground to cause current to flow through that one side of the coil to produce the step. With the Uni-Polar configuration only 1/2 of the coil is ever energized at any given time. The voltage application and stepping sequence for the Uni-Polar motor might look the the following:

6 | 1 | 4 | 5 | 8 | 7
12V | GND | Open | GND | Open | 12V
12V | GND | Open | Open | GND | 12V
12V | Open | GND | Open | GND | 12V
12V | Open | GND | GND | Open | 12V

Realize that current only flows from the center tap on pin 6 or 7 through the coil connected to ground (12V return path) producing the force to move the motor shaft. The open coil has voltage but no current flow hence no force to produce motor shaft rotation when open. With Uni-Polar stepper motors the voltage does not change to change direction of the motor shaft. Typically all that is one side can induce direction one way where the coil on the other side can induce the opposite direction or to pull onto the final stepped direction.

Converting a Uni-Polar to a Bi-Polar
Removing any voltage source from the the center tap of the each motor winding and moving it to the end of the winding then for all intensive purposes the motor becomes a bi-polar motor provided you put voltage reference on either side of the coil. Because current flows through more coil wingdings (2x) the electromotive force produced is double the force on the armature. In this way a Bi-Polar motor operation of a Uni-Polar motor will produce twice the amount of torque than operating in Uni-Polar mode because both coils are used to produce the Electro-motive force to move the motor shaft.
In the case of the moonlight focuser hi-resolution motor, leaving pin 5 open and not connecting it to 12V will produce 2x the torque for each step movement. This can be an important consideration especially thinking about moving heavy cameras, filter wheels and rotators connected to the focus tube. It would make sense to possibly wire a Uni-Polar motor in a Bi-Polar configuration. The ardumoto board applies a lead swap between the motor pins so + supply Voltage (positive lead) is on one side and return voltage path (negative lead) is on the other motor wire by changing the direction pin on the board. The enable pin is always one when driving. Therefore the motor leads on the from the ardumoto board are always a voltage source and return on the two leads.

Stepper Motor Rotation Steps
The key when selecting the stepper motor for focus application is the number of steps per revolution. The steps per revolution is probably the most critical element in assembling your electric focusing system. You have to assess how does your telescope achieve critical focus and how much change is required to move you in and out of the critical focus. You need fine step resolution in your critical focus region. You ultimately should target at least 20 motor steps through this region. Start by assessing how much do you turn your focus know manually to go just in and out of focus. Also how are you installing your focus motor. Typically the stepper motor is installed on the main rotational shaft of your focuser say for a crawford focus tube. For something like an SCT, many of worked towards using a belt drive approach. You have to ultimately assess how much motor output shaft rotation is equivalent to your manual focus rotation in the critical focus region. For many refractor and newtonian telescopes you attach the motor direct to the main high speed focus control shaft. You do not attach it to a 10:1 knob shaft as those gears are not designed to take the rotation and torques that a motor will apply. Since the motor attaches to the primary shaft, you now have to remember how much your focus changes in one full rotation of the focus knob. The faster your telescope the more critical focus range is on the focus adjustment. Think about it for a moment. If you find you go in/out of focus with 1/4 turn of the fine focus knob. This means you are changing the main shaft by 1/4 of 1/10th rotation of the main focus shaft. Mathematically this is 0.025 of one full rotation. If you look at the shaft end on and remember a circle has 360 degrees rotation, this 0.025 rotation = 9 degrees of rotation. This notation is important, because stepper movement is always expressed in degrees of rotation per step or the number of steps for a full 360 degree rotation. Every full step will move the shaft by the documented rotation specification.
If you wanted 10 finer steps to define your focus range then you would need 9deg/ 10 or 0.9 degree/rotation stepper motor. Therefore when you go to select your stepper motor you want to look very closely at the stepper motor output rotation/step specification.
For example Moonlite Telescope high resolution focus motor output output shaft rotation is 0.1 degree per step, which is also expressed as 3600 steps per revolution. This means that for that 1/4 turn of fine turn knob this motor would use 90 steps to rack in/out of focus.
Hence it becomes very important to select a stepper motor with a high number of steps per revolution to provide fine step resolution for focus placement.
If you choose to use a belt drive mechanism, don’t forget to account for the reduction gain you can achieve by using different sized belt pulley wheels in your system design.

## Full Step vs Half Step Motor Operation

To understand the differences between full step and half step, one has to visualize what must happen to make the motor shaft turn. The simplest terms is a stepper motor is a two phase motor with two electro-magnetic poles place 90 degrees from each other, relative to the motor shaft. Electric current through the a coil will produce a N-S magnetic orientation. The
key to producing the N-S pole is the current flow direction from
positive voltage to negative or zero voltage state. When current is
flowing only through 1 coil (Phase A), the armature tries to align with the field of phase A. Energizing a single coil is shown as positions 2, 4, 6 and 8 in the adjacent diagram. When current flows through both coils (Phase A and B), there are now two magnetic fields and the rotor aligns between the two poles at 45 degrees. Energizing both coils at the same time is call a full step motor movement. When both coils are energized, there is twice the magnetic field interacting with the motor rotor and hence produces the strongest motor torque. Full torque, and full step state become position 1, 3, 5 and 7 in the adjacent diagram. The
arrows at these positions are longer because the magnetic force is
stronger than if a single coil was energized.

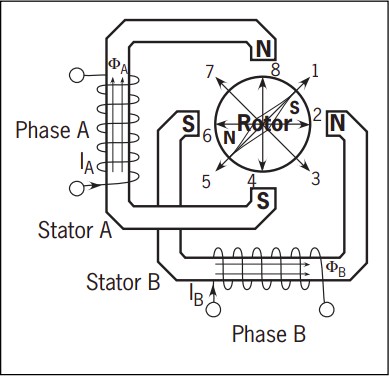
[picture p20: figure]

In order to produce motor rotation, the sequence of steps must energize the coils one direction or the other in the correct sequence to get the rotation. In the diagram full step sequence 1-3-5-7 would produce a Clockwise direction and 1-7-5-3 would produce a counter clockwise rotation. For Half steps it must be the sequential order 1-2-3-4-5-6-7-8 for clockwise and 1-8-7-6-5-4-3-2 for counter clockwise rotation. Most people fear and think connecting the wires to get the correct sequencing is hard to achieve. In actual fact, it’s easy as long as always keep the wires for each coil together.
Looking at the 28BYJ-48 Stepper motor, the truth from the data sheets identifies the following sequence. The 28BYJ-48 has two versions of either 5V or 12V which is applied to red wire for a Uni-Polar configuration. The “–“ in the truth table identifies the wire at 0 Volts to produce current flow through corresponding coil. It is important to realize stepping through step position 1 to 8 produce clockwise (CW) direction, and reverse order 8 to 1 produced counter clockwise (CCW) direction.

Figure 1: 2 Phase Stepper Motor

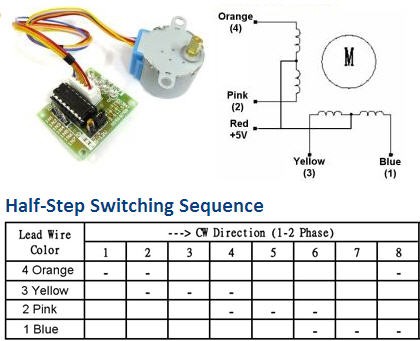
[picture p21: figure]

Figure 2: 28BJY-48 Stepper Motor
To de-mystify the wiring situation, the following is what happens when the 28BYJ-48 (12 volt version) is wired in 4 different ways to the PNP-Focus Ardumoto shield. Wires have to be connected in coil pairs where blue and yellow is one coil and orange and pink is second coil. Motor shield has motor A or B output for either coil. The table top is the Ardumoto terminal strip when viewed from the wires from left to right. All results are voltmeter measurements recorded on a bipolar connected 12V Hurst stepper motor. The LED states are on my standalone unit used two different colour LED being red (R) and yellow (Y). Te PNP-Focus Stick the Nano motor shield used same red colour so they were differentiated by Inner(I) as being closest to the terminal strip and Outer (O) being furthest away from terminal strip. The half step switching sequence is the 28BYJ-48 stepper motor state in figure 2 above where the dash represents the wire fired using a 0V state at the appropriate colour lead.

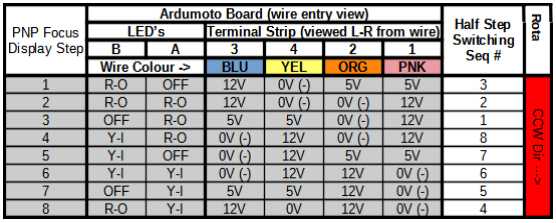
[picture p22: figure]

Figure 3: Wiring #1

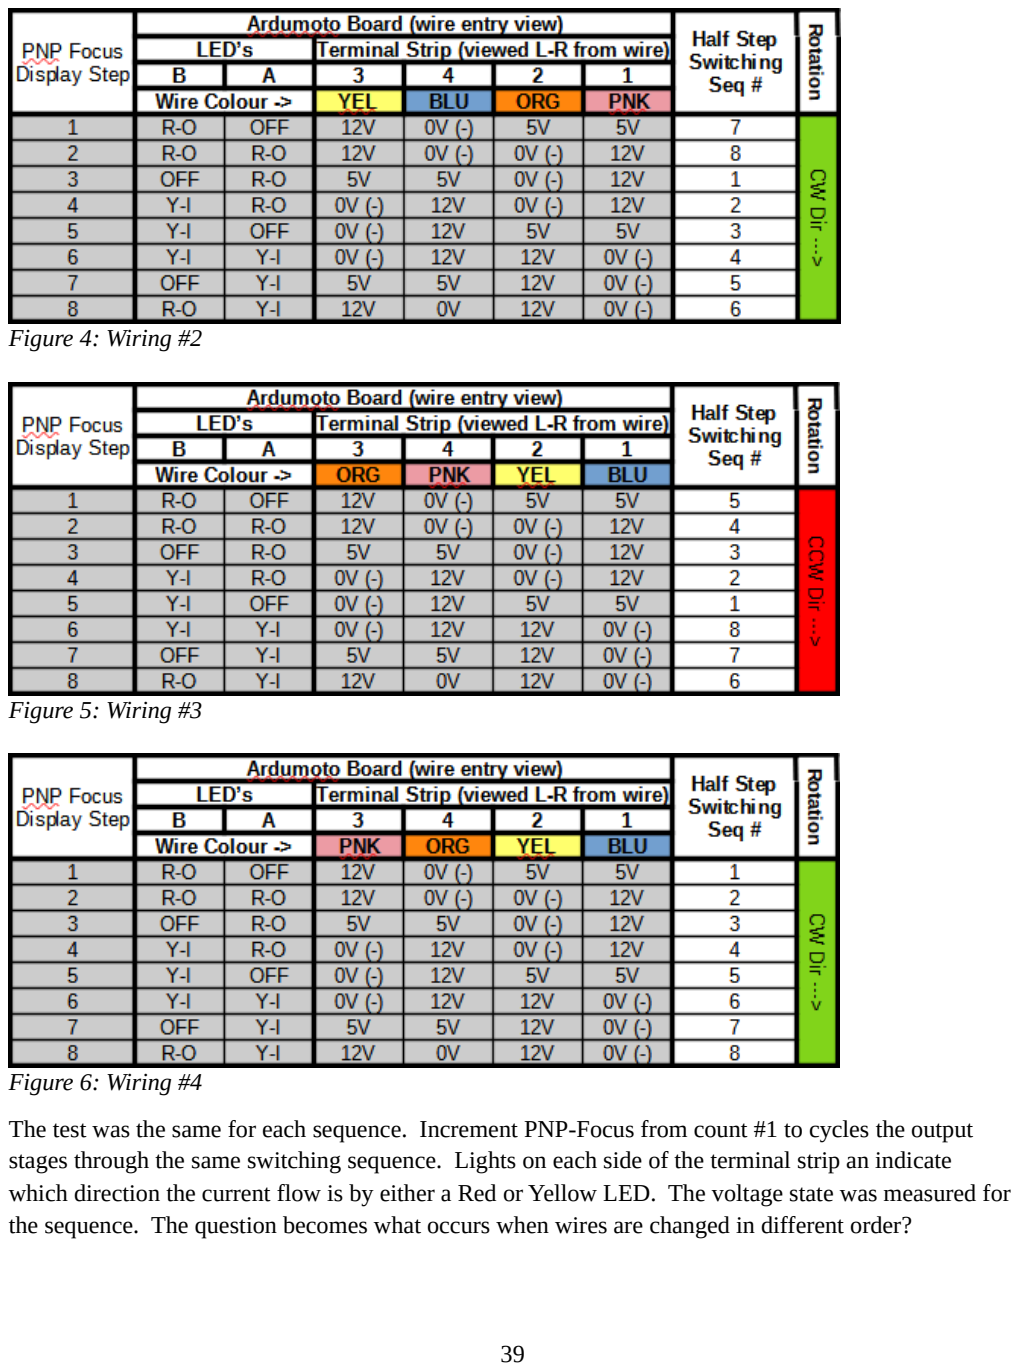
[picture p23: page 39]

Figure 4: Wiring #2

Figure 5: Wiring #3

Figure 6: Wiring #4
The test was the same for each sequence. Increment PNP-Focus from count #1 to cycles the output stages through the same switching sequence. Lights on each side of the terminal strip an indicate which direction the current flow is by either a Red or Yellow LED. The voltage state was measured for the sequence. The question becomes what occurs when wires are changed in different order?

In Wiring #1, step 1001, only the yellow wire is at 0V. Looking back at the truth table this corresponds to sequence step #3. The process is repeated for all the steps 1001 through 1008, looking at the 0V(-) correlation and recording the corresponding switching step number based on wire colour.
For wiring of blue - yellow – orange – pink sequence to the terminal, the step sequence is reduced sequentially in correct order and should produce counter clockwise (CCW) direction output on the motor shaft when counter positions are increased.
For the second test, wiring #2, the Yellow and Blue wires are swapped on the B3 and B4 output terminals to see if a valid step sequence is produced. The same sequence is performed and evaluated against the truth table. Again, a correct increasing step sequence is observed where steps complete a full proper loop. Therefore increasing display step values 1001-1008 should produce a clockwise (CW) motor shaft rotation.
For the third test, wiring #3, the pairs are swapped between output A and B, without lead swap in the coil pair to see if a valid step sequence is produced. The same sequence is performed and evaluated against the truth table. Again, like wiring #1, a correct increasing step sequence is observed where steps complete a full proper loop. Therefore increasing display step values 1001-1008 should produce a counter clockwise (CCW) motor shaft rotation.
For the fourth test, wiring #4, the orange and pink leads are swapped between output B3 and B4. The same sequence is performed and evaluated against the truth table. Again, like wiring #2, a correct increasing step sequence is observed where steps complete a full proper loop. Therefore increasing display step values 1001-1008 should produce a clockwise (CW) motor shaft rotation.
That confirms the wiring order mystery is not really a problem.
The second issue is Uni-Polar motor wiring. In all the tests above, if the red wire is connected to 12V, the lead that has 12V applied will not have any current flow to produce a N-S magnetic field. Only half of the coil, who’s lead is connected to 0v(-) will produce current flow to produce the magnetic field. The current direction remains the same in all cases as the bi-polar stepper. The only difference is when the ardumoto shield has the output disabled, both output stages go to 5V instead of 12V. The current flows through each half of the coil and is balance so the magnetic field cancels each other out. So operating as Unipoled power to the 5th lead should work the same way but only half of the possible torque.
If the Uni-Polar motor red wire is disconnected and left open. First is to notice it is tied to both coils. Using standard resistance theory, the resistance of each coil is essentially the same. A standard voltage divider is formed and if 12V is place across either yellow/blue pairs or orange-pink pairs, the red wire would have half voltage, or 6V at the lead. In full step moves, both coils are energized and both would have the lead at a 6V potential. So there is no effect. When in half step the coil energized with 12V will produce 6V on red wire, however output was measured at 5V. The drive output is at a high impedence tri-state output, hence there is no current flow through the OFF coils and no magnetic field Therefore, in summary.

- With any stepper motor, provided you ensure that both wires to a single coil wires are connected to the same motor output, A1-A2 or B3-B4, you will get a proper drive sequence. As soon as PNP-Focus drive the motor through 4 or 8 steps, it will find the correct rotational sequence to drive the motor.
- If using a Uni-Polar stepper motor, it doesn’t matter if the 5th lead is tied to voltage or not as it will still produce a correct stepping sequence.
- If a Uni-Polar stepper motor had the 5th lead tied to Vin voltage, the motor torque output will be half of what a Bi-Polar drive would be.
- If a Uni-Polar stepper motor has the 5th lead disconnected, yes there will be a voltage produced on the lead and needs to protect it from contacting other metalic surfaces or PNP-electrical circuits. However it will function like a bi-polar motor and provide about twice the torque of the Uni-Polar motor operation. This mode becomes the recommended way to drive a Uni-polar stepper motor with the PNP-Focus unit.

All sounds good, but there is a catch! Half step drive on a stepper motor may not always have consistent step responses for each half step command. At various steps, only one stepper coil is firing, therefore there is reduced torque on the output shaft. Before considering using half step operating mode ensure that you repeatedly test your whole focus system with all equipment loaded on the focus tube to ensure the focus motor can move the load. Command the position repeatedly out and in and then physically measure if the focus tube is at the same position after a minimum of at least 10 cycles. If your load exceeds the stepper motor torque you will start to loose step positions even though the count is correct because the motor actually stalls. There is a higher probability for the stepper motor to stall with your focus tube load, in which you have inconsistent focus position changes when trying to use half step operations.
Recommendation is to select a correct motor with a higher number of steps, and run at full step movements; rather than use a lower resolution stepper motor and try to run with half step movements to provide the focus resolution needed to focus your telescope. The lower step motor will no doubt have lower torque and then asking it to use half steps, then uses even less torque for each step request. It becomes a double problem when considering designing and using half stepping operation with the stepper motor.

## Backlash Compensation Considerations

With many geared stepper motors you may experience backlash situations. Backlash is simply the state that if the motor rotation changes, how much does the motor shaft have to move before it registers a change direction in the output shaft rotation. Very simple if moving from racking out how much does the motor need to turn before the focus tube start to move inward. Every system is different. Geared focus tubes can have backlash, geared stepper motors can have backlash. The easiest way to deal with backlash is to ensure focus is always approach using the same focus movement direction. The predominant telescope design has the focus tube pointing down to the ground when the telescope is pointed up at the stars. In this manner, it is always preferred to move the focus tube up to achieve focus. The effect of gravity forces all the gears to be loaded the same way when focus is achieved. When the focuser is moved outward, the focus position is required to move beyond the target position and the reverse direction and rack inward to the finished focus position. In this manner backlash is compensated. If you are manually controlling the system using standalone system, you can use the focus drive buttons to manually compensate for any backlash issues. Computer control however requires a programmed compensation approach to deal with backlash.
The Moonlite Telescope DRO focus driver does not have a value or field to enter to provide backlash compensation. The Arduino code however has the backlash compensation value. The PNP-Focus is designed around the concept that an increase in position count is moving the focuser towards the ground and further away from the telescope objective. When the ASCOM driver is commanded to move to a focus target position is greater than the current position, it will apply the backlash value to it’s first position move. Once the first position is reached the motor will reverse direction move towards the final focus position by reducing the focus position step count.
To illustrate if the current focus position is 1000 and backlash compensation value is 20; when the focus position is commanded to move to 1100, the focus motor will first drive out to 1120, stop and then move up to the final focus position of 1100. If the focus position were to move to 950, the focus would drive direct to position 950, without any overshoot. In this manner all target position have the focus moving upward to the final focus position.
Some telescopes however have focus tubes on top, where focus movements inward or smaller focus position number move in towards the ground. Example Newtonian telescopes with the focus tube on top. If you have this situation, the easy fix is to swap the stepper motor leads such that increases in focus position, actually move the focus tube inwards rather than outwards. Remember, backlash compensation will only apply to position where the target position is larger than the current position. Therefore if you configure the motor direction where increasing the number moves the focus tube inward, then start your fully racked in position at your maximum movement count. For example, say your maximum movement position is 10000, start the racked in position at 10000. Then racking the focus tube up and out of the telescope would be some number less than 10000. This way a position move to 9000 would not have backlash compensation applied. However if the next position was 9100, backlash compensation would work properly. The position change from 9000 to 9100 is moving towards the ground and towards the pull of gravity.

## Attachment to Focus Shaft

Attaching the stepper motor to your focus control shaft, has many different methods. If you are attaching to motor direct to the focus shaft, do not use a plain fixed coupler. The focus rods have a very small diameter. If the mount for the motor is not exactly perfect and the centre of the two shaft align, then no doubt the
focus control shaft will be bent. Instead use some form of
flexibile but rigid coupling between the motor and the focus
control shaft. These coupling are very rigid in rotation however they are designed to flex in x and y direction as the rotation is performed. This ensures the focus position
is accurate and that you do not have to exactly precise with the motor
installation position. The couplings come in various designs and
configuration. Many couplings have the same diameter on either side of the coupling, however many stepper motor output shaft is a different diameter than the focus control shaft diameter. Pay close attention to
the hole diameter, when ordering the motor couplings. The most
common coupling for stepper motors online is the 8mm to 5mm

coupling where 5mm will attach to the stepper motor and the 8mm is designed to attach to a 3d printer shaft. The 8mm may not be the diameter of your focus control shaft.
AliExpress (https://www.aliexpress.com/item/32911705284.html) , Amazon (https://www.amazon.ca/FULARR-Professional-Flexible-Coupling-Connector/dp/B07PCSP3KZ) , Ebay (https://www.ebay.com/b/Stepper-Motor-Coupler/181770/bn_7023350004)
Last item to consider is manual override. When you attach a geared stepper motor to a focus control shaft, you can not simply manually rotate the focus shaft know manually to move the focus. You must always use the motor drive to change the focus position. The other way to do it would be to use the Allan key and loosen the screws which connect the coupling to the focus control shaft. Moonlite Telescope found a clutch mechanism which can allow a no-tool disconnect of the focus motor to the focus control shaft. If you want to look at that approach, consider researching and using shaft to shaft clutches that can be purchased.
Shaft to Shaft Clutches: OnDrivesus.com (https://www.ondrivesus.com/shaft-couplings-clutches/clutches-up-to-100-in.lb.#1)

## User Build Stepper Motors

The following stepper motors were listed as being used with user’s build of the PNP focus controller.
Hurst ABS3008-002 | Gear Reduction: 150:1, Output Step angle 0.1°, 3600 full
steps/revolution, Coil Voltage: 12V, coils resistance: 53ohms, Coil amperage: 0.23A, Requires PNP-Focus power connection Vin=12V, used in RoboFocus Motor
Hurst Motors (http://www.hurst-motors.com/asabsgeared.html) ,
Hurst - LSG35012F76P | Gear Reduction: 75:1, Output Step angle 0.1°, 3600 full
steps/revolution, Coil Voltage: 12V, coils resistance: 65ohms, Coil amperage: 0.18A, Requires PNP-Focus power connection Vin=12V, used in Moonlite Hi-Resolution focuser
Hurst Motors (http://www.hurst-motors.com/lsg35geared.html) , Allied Electric (https://ca-en.alliedelec.com/product/hurst-nidec-motors-/lsg35012f76p/70672851/)

NEMA17 - 17HS13-0404S-PG27 Gear Reduction: 26.85:1, Output Step angle 0.067°, 5373 full steps/revolution, Coil Voltage: 12V, coil phase resistance: 30 ohms, Coil amperage: 0.4A, Requires PNP-Focus power connection Vin=12V
OMC-StepperOnline (https://www.omc-stepperonline.com/nema-17-stepper-motor-bipolar-l33mm-w-gear-raio-271-planetary-gearbox-17hs13-0404s-pg27.html) , ozrobotics.com (https://ozrobotics.com/shop/nema-17-stepper-motor-bipolar-l33mm-with-gear-ratio-271-planetary-gearbox/) Aliexpress (https://www.aliexpress.com/item/32585634347.html)

installed by TomK

28BYJ-48 – 5V Gear Reduction: 64:1, Output Step angle 0.176°, 2038 full steps/revolution, Coil Voltage: 5V, coil phase resistance: 60 ohms, Coil phase amperage: 0.09A
Note: full step motor rotation =11.25°. Most tables list sequence for half steps. Half step output resolution = 0.088° Half step output resolution = 0.088° or 4076 steps/revolution which not what will be usable.
Note2: Confirmed was able to run 28BYJ-48 – 5V on standalone PNP-Focus running strictly on USB connection to an externally powered USB hub. Operates only in Full step mode without any special wiring or soldering to the ardumoto board pins. Lot’s of torque and very quiet. The PNP-focus stick as stacked together does not provide 5V to Vin connection and will not drive the motor without modification. However soldering a wire connection between 5V and Vin pins on the Nano motor shield, confirmed it will drive the motor off the USB connection. Now to just come up with housing to put the motor and PNP-focus all in one unit and attach directly to telescope. This becomes a completely self contained focuser. Caution would be always ensure it is run off an external powered hub. https://youtu.be/u_0s6xRi2YM

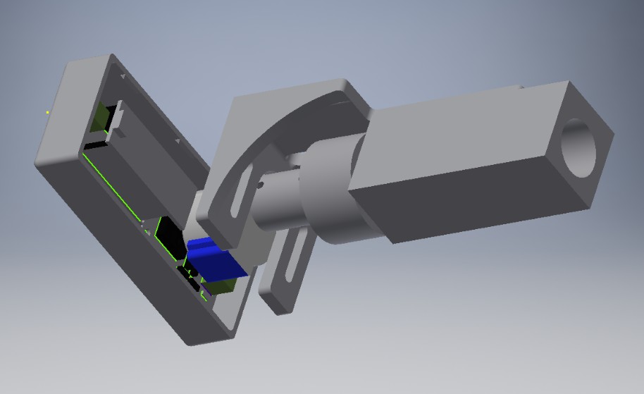
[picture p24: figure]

28BYJ-48 – 12V Gear Reduction: 64:1, Output Step angle 0.176°, 2038 full steps/revolution, Coil Voltage: 12V, coil phase resistance: 130 ohms, Coil phase amperage: 0.09A
Note: full step motor rotation =11.25°. Most tables list sequence for half steps. Half step output resolution = 0.088° or 4076 steps/revolution which not what will be usable.

## Closing Comments

Thank you to Anat for introducing the PNP-Focus project. Thank you for all who have shared their success and progress with their project build. Pictures of users ideas and project builds, greatly help in information consolidation for this document. As time moves forward many of the details and items in this document will become stale and outdated. I can envision using the Leonardo and two Ardumoto shields to build a headless focus and rotator controller as a possible future adaptation. It would have to be headless because the LCD1602 shield used too many pins that would be needed to drive a second Ardumoto shield.

I hope this document will encourage you to take on your own PNP-focus controller project and that you will find success with your PNP-Focus controller.

Sincerely,
Todd Benko

## Technical Reference

## L298P 2A Dual Channel DC Stepper Motor Driver Shield Module For Arduino Nano 3.0

The NANO Motor Shield is based on the L298P, which is a dual full-bridge driver designed to drive inductive loads such as relays, solenoids, DC and stepping motors. It lets you drive two DC motors with your Arduino NANO board, controlling the speed and direction of each one independently. You can also measure the motor current absorption of each motor, among other features.

•You can find in the Getting Started section all the information you need to configure your board, use the Arduino Software (IDE), and start tinker with coding and electronics.
Technical specs
Operating Voltage | 5V to 12V (See specification caution below)
Motor controller | L298P, Drives 2 DC motors or 1 stepper motor
Max current | 2A per channel or 4A max (with external power supply)
Current sensing | 1.65V/A
Free running stop and brake function

Power
The NANO Motor Shield must be powered only by an external power supply. Because the L298 IC mounted on the shield has two separate power connections, one for the logic and one for the motor supply driver. The required motor current often exceeds the maximum USB current rating.
External (non-USB) power can come either from an AC-to-DC adapter (wall-wart) or battery. The adapter can be connected by plugging a 2.1mm center-positive plug into the Arduino's board power jack on which the motor shield is mounted or by connecting the wires that lead the power supply to the Vin and GND screw terminals, taking care to respect the polarities.
To avoid possible damage to the Arduino board on which the shield is mounted, we reccomend using an external power supply that provides a voltage between 7 and 12V. If your motor require more than 9V we recommend that you separate the power lines of the shield and the Arduino board on which the shield is mounted. This is possible by cutting the "Vin Connect" jumper placed on the back side of the shield. The absolute limit for the Vin at the screw terminals is 18V.
The shield can supply 2 amperes per channel, for a total of 4 amperes maximum.
(See caution specification below about power considerations)

Input and Output
This shield has two separate channels, called A and B, that each use 4 of the Arduino pins to drive or sense the motor. In total there are 8 pins in use on this shield. You can use each channel separately to drive two DC motors or combine them to drive one bipolar stepper motor. The shield's pins, divided by channel are shown in the table below:
Function | pins per Ch. A | pins per Ch. B
Direction | D12 | D13
PWM | D3 | D11
Brake | D9 | D8
Current Sensing | A0 | A1

If you don't need the Brake and the Current Sensing and you also need more pins for your application you can disable this features by cutting the respective jumpers on the back side of the shield.
Motors Connection

Brushed DC motor. You can drive two Brushed DC motors by connecting the two wires of each one in the (+) and (-) screw terminals for each channel A and B. In this way you can control its direction by setting HIGH or LOW the DIR A and DIR B pins, you can control the speed by varying the PWM
A and PWM B duty cycle values. The Brake A and Brake B pins, if set HIGH, will effectively brake the DC motors rather than let them slow down by cutting the power. You can measure the current going through the DC motor by reading the SNS0 and SNS1 pins. On each channel will be a voltage proportional to the measured current, which can be read as a normal analog input, through the function analogRead() on the analog input A0 and A1. For your convenience it is calibrated to be 3.3V when the channel is delivering its maximum possible current, that is 2A.

Specification Caution
These reference notes appeared to be copied from many of the Ardumoto documentation. The silkcreen on the back of the board clearly states DC7-12V but yet documentation talks about Vin max of 18v.

A little more reverse engineering on the Nano motor shield board:
The Vin connection at the terminal strip passes through a reverse protection diode and then 2 filtering capacitors. The electrolytic capacitor is rated for 25v. The trace then jumps through the board and runs parallel A2 pin all the way to the Vin pin before making a trace connection to Vin. There is no Vin Connect jumper to be able to cut a trace to separate V-in from the Arduino micro controller as the documentation discribes.

looking at the chips:
LM358 (Closest to the electrolytic capacitor) datasheet specifies operating voltage 3-32V. OK CD4077BM datasheet specifies DC supply range -0.5 to 20V OK
L298P datasheet specifies Vs input supply 50v Max OK.

Appears that all the chips on the motor control can handle voltages up to 20v. Therefore a 18V Vin would be a safe bet. So the problem clearly is the Vin connection to the Arduino Micro board

My gut feeling is 5V voltage regulator on the Arduino Micro probably can not handle voltages in the 14v range. Since there is no simple disconnect of Vin on the micro board they labelled the V-in range 7-12V as recommended in arduino documentation.

Anyone see a problem developing here? People might be running their mount of a battery system with a charger applied to the battery. Typical battery charger will set voltage at 14.2V. So far I haven't seen this to be a problem with the standalone version. I have run my mount from a portable jumper pack and had it plugged into AC power and charging while it is running my whole mount and astro-photo rig. It didn't create any problem for the Stand alone version.

The Arduino Micro doesn't have a Vin barrel connection, and since we are using it strictly as computer connection, we need to seriously look at the Vin connection. It serves no purpose to have Vin connection from the Nano motor shield to the Micro. The Micro can be powered up and driven totally by the USB port. Therefore with the PNP-focus Stick, do not install a connector pin on the Arduino Micro Vin connection.

To drive the 5V version of the 28BYJ-48 stepper with the PNP-stick, we can simply solder a jumper between 5V and Vin on the back of the nano motor shield. So far I haven't had any problem driving the 28BYJ-48 from USB provided it is connected to an external powered USB hub.

## Revision Notes:

Version 2.0.2: Bug Fix. On position changes less than 250 steps, the motor would start at step speed set to the number of position change steps with no acceleration. Fixed the whole acceleration logic to determine if position change within the Ramp range and the ASOM commanded speed before applying increase or decrease to step speed.
Version 2.0.1: Fix a bug, where runs longer than 30 seconds would cause motor to halt abruptly and then start back up. Issue was caused by temperature sample taken at 30 second interval, which interrupted the motor move sequence. Also removed dependency on requiring steps per revolution. Original stepper motor library based speed decisions on RPM. During discussion on forum thread about what speed to used on belt drive design discussion, I realized that setting speed to Ascom driver speed selection differed with use of RPM speed calculated results. As result converted stepper motor to strictly use steps/second velocity to determine step timing interval rather than RPM and eliminated need to enter any motor step information. Half step motor drive problem had been reported, confirmed the motor drive sequence did not fire in the same sequence as documented in manual for the 28BYJ48 motor. Added further documentation to program and to this document about LED signals and corrected firing sequence. Concern is that different stepper motors may require different firing order sequence for half step operation. Hopefully half step order control is not manufacture dependant. Also changed the start start and stop operations to a fully ramped speed control rather than a 4 step speed control change to provide a much smoother transition from starting and target position changes.
Version 2: As a result of not being able to have the firmware recognized by the Moonlight DRO focus ASCOM driver, I decided to take on the task of revamping the whole Arduino firmware and interface was developed. I didn’t like the way the code was structured. The previous code had so many limitations and did not fully implement Moonlite DRO ascom driver features.
In testing the new version, it became apparent that sometimes the PNP-Focus would be detected by the Moonlite DRO ASCOM driver as a 2 driver board version. Code was installed to respond for 2 driver version. Later it was determined that it might not be needed because of the specified version response to the driver and was commented out. One of the first tasks was elimination of the delay command for use in many of the areas which was slowing down the Arduino execution. Another goal was to make the code adaptable so the same code could be used to load both the standalone PNP-Focus board and the PNP-Focus stick rather than having separate versions. In addition it would allow the PNP-Focus board to run headless without the LCD1602 Shield if a person decided not to install. Another of the key features was ensure the unit was fully compliant with how the Moonlite DRO driver worked. I discovered that while some commands were available in the driver listing, Moonlite Telescopes didn’t necessarily implement the function in the device and firmware. Key elements included speed control which matched the driver, setting and reporting proper speed control. The original driver used a fixed speed that was not controlled by the driver. In managing the interface to the Moonlite commands in the DRO driver, a Moonlite command library was added to the project. Further enhancements developed included configuring the data display to display more useful information and expanded functionality.

Expanding but also simplifying the display button control with more brightness levels. The addition of ramping manual speed control which eliminated the need to manually change speed. The new code totally made use of the stepper timing for specific speed based on steps per second rather than simply using time delays. The ardumoto library was fixed properly so the correct speed would be based on the number of steps per rotation of the stepper motor. In addition when a move was completed, the motor drive outputs would be disabled, ensuring the motors didn’t need to heat up when not moving. Full step and half step stepper mode was implemented with corrections again to library code that was previously conceived. Also included the ability to provide backlash compensation for focus rack-out position changes. Also it was recognized that the higher Moonlite speed levels have been known to cause focus tube slippage with heavy photography equipment loads on the focus tube. To address this problem, both soft start position change and slower target position settling speeds were added. Now higher ASCOM speed settings can now be used without compromising positional accuracy and repeatability. In essence, the firmware was totally re-written and restructured. The main loop now contains only a small repeatable core set of element actions removing all the uncessary delays to the firmware cycle time. Because there are so many significant code and functional changes, this version is re-branded as PNP-Focus V2.

Version 1 variations: These versions had their simple firmware configuration based on work started by Orly Andico and the cloudy nights thread started by Anat Ruangrassamee. There have since been 5 other firmware versions spawned where people have adapted the code to their specific purpose and shared. The problem with many of these older versions is that many would not be detected by the new Moonlite DRO focus ASCOM driver.

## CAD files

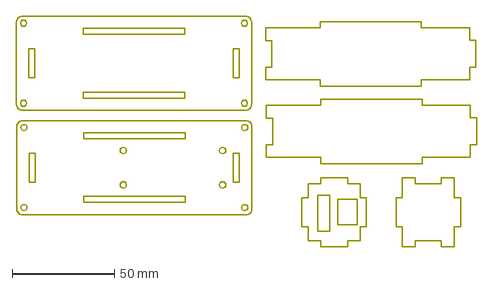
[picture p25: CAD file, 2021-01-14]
lasercut_PnP_Focus_Stick.dxf
224.7 x 112.7 mm

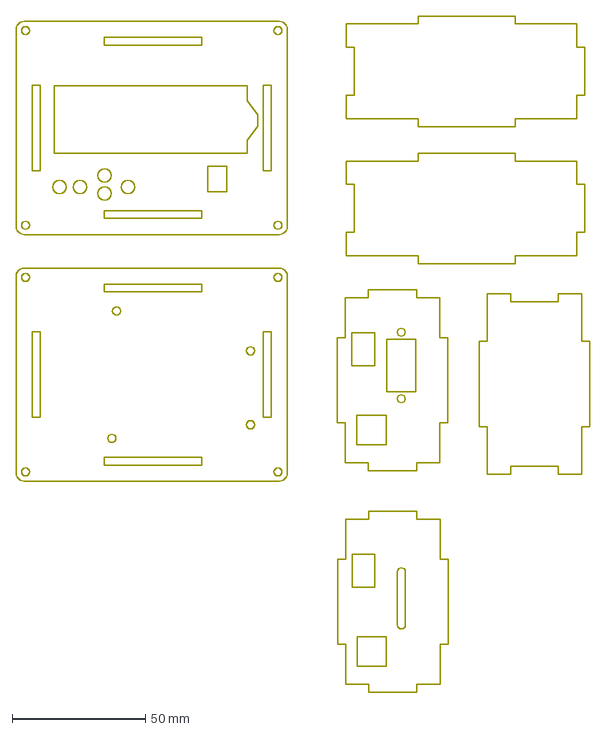
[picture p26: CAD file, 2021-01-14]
lasercut_PnP_Focus.dxf
215.4 x 253.8 mm

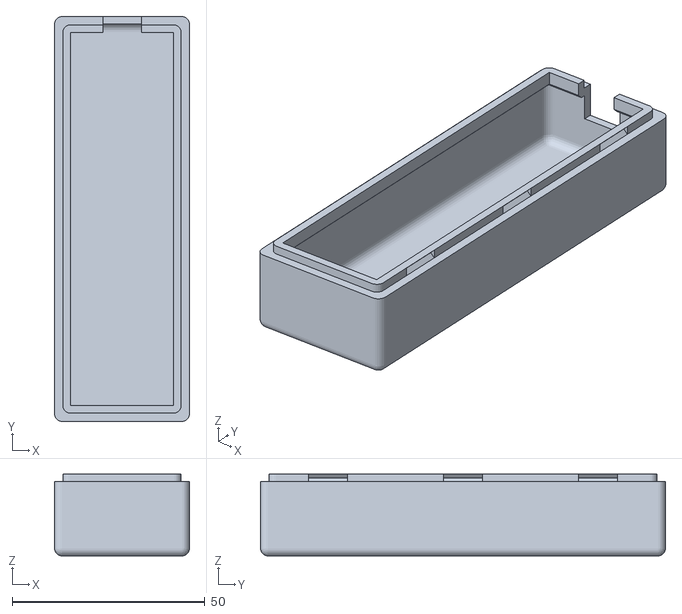
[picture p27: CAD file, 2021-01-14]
StickCaseBottom.stl
35.0 x 105.0 x 21.3

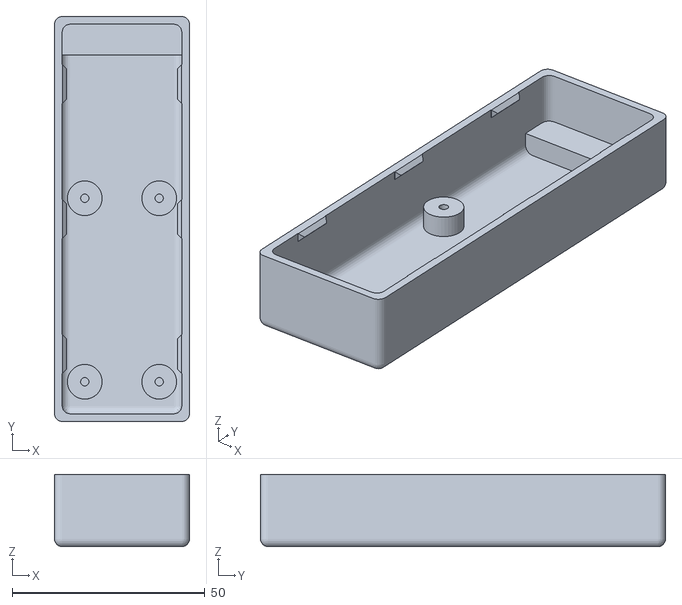
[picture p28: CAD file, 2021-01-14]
StickCaseTop.stl
35.0 x 105.0 x 18.8

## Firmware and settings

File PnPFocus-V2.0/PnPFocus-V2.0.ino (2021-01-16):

//  PnP-Focus Controller
// 
//  Moonlite-compatible stepper controller
//
//  Original code by orly.andico@gmail.com, 13 April 2014
//  Modified by Anat Ruangrassamee (aruangra@yahoo.com), 26 September 2017
//  Modified V2.0 by Todd Benko (Dtdastro@gmail.com), 01 November, 2020
//  Modified V2.0.1 by Todd Benko, 14 January 2021  - remove need for steps per revolution and ardumoto library now speed based using steps/s, 
//                  fix pause that was occuring at 30 second run, re-order half step based on 28BYJ-48 motor table, change step speed change to ramp speed change
//  Modified V2.0.2 by Todd Benko 16 January 2021 - Fix no acceleration on steps < 250
//
//*****************************************************************************************************************************************************************
//  USER NOTIFICATION
//  
//  Ardumoto board can be purchased with different pin assignments 
//  The standard for this programs uses
//  D3 -A motor PWM drive 
//  D11-B motor PWM Drive
//  D12-A Dir
//  D13-B Dir
//  If your Ardumoto board uses different pin assignment, you must change assignment in to match in ArdumotoStepper.cpp
//  program is default setup to work with 
//  ardumoto shield which uses pins 3,11,12,13
//  nano motor shield which uses pins 3,11,12,13
//  
//  Many of the ardumoto boards do not have the logic voltage selection applied.  The Leonardo uses 5V logic.
//  A solder connection must be made to the 5V pad on the logic-V selection pad on the Ardumoto board.  
//  Nano Motor shield already has 5V logic selected.  The ardumoto library only provides full step operations 
//  because the dir pin is what swaps polarity of both coils on the stepper wire and there is no individual control of each stepper coil
//  
//  Program tested to work with both the 
//  Leonardo AVR board
//  MICRO AVR board
//  
//  Program can be used with various Arduino boards provided you select the correct board in Tools-Board menu and
//  which serial port connected in Tools-Port selection
//  
//  The following are usable definitions which can be changed to match your specific devices and assembly configuration
///////////////////////////////////////////////////////////////////////////////////////////////////////////////////////
///////////////////////////////////////////////////////////////////////////////////////////////////////////////////////
//
// USER CONFIGURATION AREA
// Set the following program variable states and code lines specific to your build and choice of operation.

// Enable Half step mode
const bool enableHalfStepMode =  true;                // If stepper motor stalls/studders in half step mode, can disable half step mode so only full step is selected.
                                                      // true = half and full step modes available, 
                                                      // false = only full step mode is enabled.

// Backlash Compensation: Many geared focus motors have backlash in the gears when changing direction.  The motor shaft must turn x number of steps before the output shaft will turn.
// The way around the backlash problem is to always approach the target focus position from the same direction.  Backlash compensation is applied to focus movements that extend the 
// focuser position. The backlash compensation only apply to ASCOM driver target position changes.   When the focuser is racked outward the focus position will overshoot the 
// target position  by the backlashValue amount and then be racked back in to the target position.  This approach provide constant approach to the focus position and 
// removes the backlash in the gears and removes gravitational effects on position change.  
const unsigned short backlashValue=0;                 // increase this value to have a positive overshoot and rack back in to compensate for focuser backlash. 
                                                      // zero implies no backlash, value of 10 will rack out  10 additonal steps and the 10 steps 
                                                      // inward to finish at the target position.

// Temperature reporting values in which format  default is Celcius
const bool displayFahrenheit = false;                  // false =  temperatures in Celsius., true = temperatures in Fahrenheit.


// LCD1602Shield settings 
// if the LCD1602 display shield is installed following line should be #define LCD1602Shield , if not installed it should be //#define LCD1602Shield 
// For Leonardo standalone build with LCD1602 shield installed, the following line needs to be #define LCD1602Shield
// For Leonardo standalone build with LCD1602 shield NOT installed, the following line needs to be //#define LCD1602Shield
// For PNP-focus Stick next line needs to be //#define LCD1602Shield 
//#define LCD1602Shield   

// LCD1602 starting brightness at powerup for StandAlone unit
const short userStartBrightness = 100;                  // for standalone unit Change value to personal choice for startup brightnes 0=off 10= dim 200= bright  value range is 0 to 255



////////////////////////////////////////////////// 
//   END OF USER CONFIGURATION AREA
//   Do not change anything beyond this point 
//   unless you wish to embark on Arduino programming 
///////////////////////////////////////////////////////////////////////////////////////////////////////////////////////
///////////////////////////////////////////////////////////////////////////////////////////////////////////////////////

// Programming note:  Following are code block examples which are used to apply code to be compiled if LCD shield is are installed
#ifdef LCD1602Shield  
  // code which will be compiled for use when LCD1602 shield is installed
#endif  // LCD1602Shield

////////////////////////////////////////////////////////////
// Common Libraries includes and intializations declarations
////////////////////////////////////////////////////////////
#include <EEPROM.h>
#include "Moonlite.h"                             // use serial commands to communicate with moonlite driver
#include "ArdumotoStepper.h"                      // use the ardumoto shield or nano motor shield
#include "OneWire.h"                              // use one wire protocol for dallas temperature sensor
#include "DallasTemperature.h"                    // use dallas temperature sensors DS18B20, or DS18B22, or DS18B25
#include <LiquidCrystal.h>                        // use the 1602 LCD display shield

// Definitions


///////////////////////////////////////////////////////////
// Temperature Sensor connection
///////////////////////////////////////////////////////////
#define           ONE_WIRE_BUS A2                 // Data wire is plugged into pin A2 on the Arduino  Needed to move temperature to A2 because Nano shield used A0 and A1.
OneWire           oneWire(ONE_WIRE_BUS);          // Setup a oneWire instance to communicate with any OneWire devices (not just Maxim/Dallas temperature ICs)
DallasTemperature sensors(&oneWire);              // Pass oneWire reference to Dallas Temperature.

///////////////////////////
// Temperature Signals
///////////////////////////
float             tempC = 0;                      // temperature C reading from DS18B20
int               tempInitiated = 0;              // Temperature request initiated

///////////////////////////
// Ascom Serial Protocol
///////////////////////////
Moonlite SerialProtocol;



///////////////////////////
// Motor Control Signals
///////////////////////////
int               isRunning = 0;                  // variable to manage if ASCOM move loop is running
unsigned short    stepSpeed = 2;                  // display speed holder in steps/sec
unsigned short    stepSpeedCommand=16;            // Ascom command speed holder in steps/sec
long              distanceToGo = 0;               // focuser commanded position
long              currentPosition = 0;            // focuser current position
long              targetPosition = 0;             // focuser target position from serial command
long              runningStartPosition=0;          // focus start position for serial command to control speed ramping
int               runningInitialized = 0;         // running loop initialized
unsigned short    backlashState=0;                // backlash state controller 0= completed or not required, 1= backlash rackout, 2= backlash rackin to target position
bool              motorActive=false;              // track if motor drive output is active
bool              ascomFullStep=true;             // used to keep track of ascom commanded step mode.  Always start with full mode
bool              ascomModeSet=false;             // if ascom sets mode, manual buttons can not change

///////////////////////////
// Stepper
///////////////////////////

ArdumotoStepper myStepper;                      //declare Ardumoto Stepper to MyStepper

///////////////////////////
// Timer
///////////////////////////
long temperature_millis = 0;    // minute timer for updating readings 
long lastMotorRunMillis = 0;    // timer from when the last motor move was completed.
long buttonPressMillis = 0;     // timer for managing button press debounce rather than delay in program



#ifdef LCD1602Shield  // Code if LCD Shield installed
///////////////////////////
// LCD 1602 shield initialization and subroutines
///////////////////////////
/*
 * 1602 Shield uses the following pin assignments
 * D4-LCD D4
 * D5-LCD D5
 * D6-LCD D6
 * D7-LCD D7
 * D8-LCD Reset
 * D9-LCD Enable
 * D10-LCD BackLight
 * A0 - Buttons
 * Button readings have two different analog ranges depending on which version is purchased.  
 * Need to select using comments // which pin assignment works for your LCD shield in read_LCD_buttons() function
 */
LiquidCrystal lcd(8, 9, 4, 5, 6, 7);    // select the pins used on the LCD panel

// define some values used by the panel and buttons
unsigned int lcd_key         = 0;
unsigned int adc_key_in      = 0;
unsigned int btnHoldCount    = 0;          // counter if button is being held
unsigned short flg_mode      = 0;          // control stepper mode Full or Half steppin
unsigned short flg_lcdlight  = 0;          // control display brightness
String topline = "PnPFocus        ";       // Standard top line display


#define btnRIGHT  0
#define btnUP     1
#define btnDOWN   2
#define btnLEFT   3
#define btnSELECT 4
#define btnNONE   5

///////////////////////////
// LCD 1602 Subroutines and Functions
///////////////////////////

/////////////////////////////////////
// Display text at xposition, yposition and number of mS to delay after the text is written.
// Delay actually causes the program to stop and miss serial commands.  
// Use delay sparingly
/////////////////////////////////////
void displayText (int xpos, int ypos, String displayText,int delayPeriod)
{
    lcd.setCursor(xpos,ypos);             // set the LCD cursor   position 
    lcd.print(displayText);              // print message on the LCD
    delay (delayPeriod);
}   // end display Text

/////////////////////////////////////
// display the current motor step position counter
/////////////////////////////////////
void displayPosition()
{
      displayText (0, 1, "CP:     ", 0);
      displayText (3, 1,String(currentPosition),0);
}
/////////////////////////////////////
// display the ASCOM Target position
/////////////////////////////////////
void displayTarget()
{
        displayText (0, 0, "TP:     ",0);
        displayText (3, 0, String(targetPosition),0);
}

/////////////////////////////////////
// display current temperature sensor reading results
/////////////////////////////////////
void displayTemp (float temp)
{ displayText (9,1,"     ",0);       
  if ((temp < -50) || (temp > 50)){
        displayText(9,1,"T:N/A",0);
  } else {
        if (displayFahrenheit)
        {
          displayText(9,1,"T:"+ String(round(sensors.toFahrenheit(tempC))) + "F",0);   
        } else 
        {
          displayText(9,1,"T:"+ String(round(tempC)) + "C",0);   
        }
  } 
} // end displayTemp

/////////////////////////////////////
// turn ON drive power display indicator
/////////////////////////////////////
void displayStepperPowerOn ()
{
  if (myStepper.getStepMode() == FULLSTEP)
    displayText(15,1,"F",0);
  else
    displayText(15,1,"H",0);
}

/////////////////////////////////////
// turn OFF drive power display indicator
/////////////////////////////////////
void displayStepperPowerOff ()
{
  displayText(15,1," ",0);
}


/////////////////////////////////////
// display the button value diagnotics
// input is the unsigned In reading of pin A0
/////////////////////////////////////
void displayButtonValue(unsigned int buttonValue)
{
        displayText (0, 0, "BV:     ",0);
        displayText (3, 0, String(buttonValue),0);
}

int read_LCD_buttons()
{  // read the buttons
  
    adc_key_in = analogRead(0);                       // read the value from the sensor 
    //displayText (12, 0, String(adc_key_in), 0);     // used for troubleshooting
   
    // my buttons when read are centered at these valies: 0, 144, 329, 504, 741
    // we add approx 50 to those values and check to see if we are close
    // We make this the 1st option for speed reasons since it will be the most likely result

    if (adc_key_in > 850) 
    {
      return btnNONE;                                   // fisrt check totally bypass all assessment if button is not pressed.
    }
    else // button is pressed
    {
      delay(2);                                         // switch debounce delay. Increase this delay if incorrect switch selections are returned.
      if (adc_key_in != analogRead(0)) return btnNONE;  // double checks the keypress. If the two readings are not equal after debounce delay, it tries again.
 
      // yes button still pressed after 10ms and button reading is still the same value execute the button
      // For V1.1 us this threshold
      /*
      if (adc_key_in < 50)   return btnRIGHT;  
      if (adc_key_in < 250)  return btnUP; 
      if (adc_key_in < 450)  return btnDOWN; 
      if (adc_key_in < 650)  return btnLEFT; 
      if (adc_key_in < 850)  return btnSELECT;  
      */
     // For V1.0 comment the other threshold and use the one below:
   
     if (adc_key_in < 50)   return btnRIGHT;//increase value
     if (adc_key_in < 195)  return btnUP;   //screen ON/OFF
     if (adc_key_in < 380)  return btnDOWN; //No Activity
     if (adc_key_in < 555)  return btnLEFT; //Decrease value
     if (adc_key_in < 790)  return btnSELECT; //Stop and save

    return btnNONE;                // when all others fail, return this.
        
  }
}  // end read_LCD_buttons

void buttonAction (int buttonCode)
{
  switch (buttonCode)
   {             
       case btnRIGHT:
         if (isRunning == 0) { 
            buttonSpeed(btnHoldCount);
            buttonMove(1);
            btnHoldCount++;
         }
         break;
       case btnLEFT:
         if (isRunning == 0) { 
            buttonSpeed(btnHoldCount);
            buttonMove(-1);
            btnHoldCount++;
         }
         break;    
       case btnUP:
             flg_lcdlight++;
             switch (flg_lcdlight){
              case 0:
                  break;       
              case 1:
                  setBrightness (0);
                  break;
              case 2:
                  setBrightness (1);
                  break;
              case 3:
                  setBrightness (5);
                  break;
              case 4:
                  setBrightness (20);
                  break;
              case 5:
                  setBrightness (200);
                  flg_lcdlight=0;
                  break;              
             }
             delay (300);    // note holding button down will cycle through the values in 1.5 seconds
             break;
       case btnDOWN:
            if (enableHalfStepMode)
            {
             if (ascomModeSet == false) 
               { 
                 if (myStepper.getStepMode()==FULLSTEP) 
                    changeStepMode(HALFSTEP);
                 else
                    changeStepMode(FULLSTEP);          
               }
               delay (500);    // note holding button down will cycle through the values in 1.5 seconds             
            }
                break;
       case btnSELECT:
             isRunning = 0; // STOP
             // EEPROM HERE
             EEPROMWritelong(0, currentPosition);
             EEPROM.write(4, myStepper.getStepMode());
             displayText (0, 0, "STOPPED & SAVED ", 1000);      
             displayText (0, 0, topline, 0); 
             displayTemp (tempC);  
             break;
       case btnNONE:
             break;
   }      
} // end buttonAction


/////////////////////////////////////
// button speed controller 
// input is number of steps taken so far with button pressed
/////////////////////////////////////
void buttonSpeed(unsigned int count)
{
  switch (count)
  {
    case 0 :
        setFocusStepSpeed(2);
        break;
    case 10:
        setFocusStepSpeed(10);
        break;
    case 50:
        setFocusStepSpeed(50);
        break;
    case 300:
        setFocusStepSpeed(100);
        break;
    case 700:
        setFocusStepSpeed(200);
        break;
  }
}

///////////////////////////////////////
// function to move motor by 1 position when button is pressed
// x input is 1 to increase and -1 to decrease current position
///////////////////////////////////////
void buttonMove(int x)
{
    currentPosition=positionChange(currentPosition, x);
    displayStepperPowerOn();                      // Turn on the motor active display tag
    displayPosition();                            // Display Current Position
    myStepper.step(x);
    lastMotorRunMillis=millis();                   // reset last motor movement timer
}

/////////////////////////////////////
// set the brightness of the display
// input 0-255
/////////////////////////////////////
void setBrightness (short bright)
{
  if(bright <0) bright = 0;
  if(bright >255) bright =255; 
  analogWrite(10, bright);
}

#endif  // LCD1602Shield


///////////////////////////
// Common Subroutines and Functions
///////////////////////////
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
void loop()
{
   
    #ifdef LCD1602Shield                      // Compile and perform following code if LCD Shield installed
      //displayText (0, 0, String(millis()), 0);            // only used for troubleshooting to see if programs is halted
      lcd_key = read_LCD_buttons();           // read the buttons
      buttonAction(lcd_key);                  // action on button press
    #endif  // LCD1602Shield
    if (isRunning) {                          // perform target moves if required
      moveToTarget();
    }else {
      temperature_action ();                    // perform temperature action if required  ensure temperature action is not performed during a move otherwise it stops the move on long moves
      if (runningInitialized !=0) runningInitialized = 0;     // Reset runningInitialized if the case of an abort;
    }
    motorIdleActions((millis() - lastMotorRunMillis));
    SerialProtocol.Manage();
    if (SerialProtocol.isNewCommandAvailable()){
      processCommand();
    }
} // end loop

/***********************************************************************************
 * Reference
 */

// Moonlite-compatible stepper controller
//
//1  2 3 4 5 6 7 8
//: C #             N/A         Initiate a temperature conversion; the conversion process takes a maximum of 750 milliseconds. The value returned by the :GT# command will not be valid until the conversion process completes.
//: F G #           N/A         Go to the new position as set by the ":SNYYYY#" command.
//: F Q #           N/A         Immediately stop any focus motor movement.
//: G C #           XX#         Returns the temperature coefficient where XX is a two-digit signed (2’s complement) hex number.  (not issued in F/W V13)
//: G D #           XX#         Returns the current stepping delay where XX is a two-digit unsigned hex number. See the :SD# command for a list of possible return values.
//: G H #           00# OR FF#  Returns "FF#" if the focus motor is half-stepped otherwise return "00#"
//: G I #           00# OR 01#  Returns "00#" if the focus motor is not moving, otherwise return "01#"
//: G N #           YYYY#         Returns the new position previously set by a ":SNYYYY" command where YYYY is a four-digit unsigned hex number.
//: G P #           YYYY#         Returns the current position where YYYY is a four-digit unsigned hex number.
//: G T #           YYYY#         Returns the current temperature where YYYY is a four-digit signed (2’s complement) hex number.
//: G V #           DD#         Get the version of the firmware as a two-digit decimal number where the first digit is the major version number, and the second digit is the minor version number.
//: S C X X #       N/A         Set the new temperature coefficient where XX is a two-digit, signed (2’s complement) hex number.
//: S D X X #       N/A         Set the new stepping delay where XX is a two-digit, unsigned hex number. Valid values to send are 02, 04, 08, 10 and 20, which correspond to a stepping delay of 250, 125, 63, 32 and 16 steps per second respectively.
//: S F #           N/A         Set full-step mode.
//: S H #           N/A         Set half-step mode.
//: S N Y Y Y Y #   N/A         Set the new position where YYYY is a four-digit unsigned hex number.
//: S P Y Y Y Y #   N/A         Set the current position where YYYY is a four-digit unsigned hex number.
//: + #             N/A         Activate temperature compensation focusing.   (not issued in F/W V13)
//: - #             N/A         Disable temperature compensation focusing.    (not issued in F/W V13)
//: P O X X #       N/A         Temperature calibration offset, XX is a two-digit signed hex number, in half degree increments.

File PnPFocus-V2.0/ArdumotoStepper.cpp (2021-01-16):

/*
 * ArdumotoStepper.cpp - ArdumotoStepper library for Wiring/Arduino - Version 1.0
 *
 * Based on Arduino Stepper library. Original Contributors:
 * Original library        (0.1)   by Tom Igoe.
 * Two-wire modifications  (0.2)   by Sebastian Gassner
 * Combination version     (0.3)   by Tom Igoe and David Mellis
 * Bug fix for four-wire   (0.4)   by Tom Igoe, bug fix from Noah Shibley
 * High-speed stepping mod         by Eugene Kozlenko
 * Timer rollover fix              by Eugene Kozlenko
 * Five phase five wire    (1.1.0) by Ryan Orendorff
 *
 * ArdumotoStepper adaptation (1.0) by Alayn Gortazar (Barnetik Koop. Elk. Txikia)
 *
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
 *
 * Drives a bipolar with 4 wires Stepper motor.
 *
 * When wiring multiple ArdumotoStepper motors to a microcontroller, you quickly run
 * out of output pins, with each motor requiring 4 connections.
 *
 * By making use of the fact that at any time two of the four motor coils are
 * the inverse of the other two, the number of control connections can be
 * reduced from 4 to 2 for the unipolar and bipolar motors.
 *
 * The sequence of control signals for 4 control wires is as follows:
 *
 * Step C0 C1 C2 C3
 *    1  1  0  1  0
 *    2  0  1  1  0
 *    3  0  1  0  1
 *    4  1  0  0  1
 *
 *
 * The sequence of halfstep control signals for 4 control wires is as follows:
 *  Step C0 C1 C2 C3
 *     1  1  0  1  0  where 1 = 0v and 0=+Vc
 *     2  0  0  1  0
 *     3  0  1  1  0
 *     4  0  1  0  0
 *     5  0  1  0  1
 *     6  0  0  0  1
 *     7  1  0  0  1
 *     8  1  0  0  0
 *
 *
 *
 * The sequence of controls signals for 2 control wires is as follows
 * (columns C1 and C2 from above):
 *
 * Step C0 C1
 *    1  0  1
 *    2  1  1
 *    3  1  0
 *    4  0  0
 *
 * The circuits can be found at
 *
 * http://www.arduino.cc/en/Tutorial/ArdumotoStepper
 */

#include "Arduino.h"
#include "ArdumotoStepper.h"

 /*
  *   constructor for four-pin version
  *   Sets which wires should control the motor.
  */
ArdumotoStepper::ArdumotoStepper()
{
    this->step_number = 0;                    // which step the motor is on
    this->direction = 0;                      // motor direction
    this->last_step_time = 0;                 // time stamp in us of the last step taken
    this->number_of_steps = 8;                // total number of steps for the sequence

    // Arduino pins for the motor control connection:
    this->motor_pin_1 = 3;
    this->motor_pin_2 = 11;
    this->motor_dir_1 = 12;
    this->motor_dir_2 = 13;

    this->stepmode = FULLSTEP;  //  Always initialize in fullstep mode  so that number of steps is based on full steps and does not change

    // setup the pins on the microcontroller:
    pinMode(this->motor_pin_1, OUTPUT);
    pinMode(this->motor_pin_2, OUTPUT);
    pinMode(this->motor_dir_1, OUTPUT);
    pinMode(this->motor_dir_2, OUTPUT);
}

/*
 * Sets the speed in revs per minute
 *   input whatspeed = motor rpm
 *   output step_delay = usec/step
 *   
 *   Change 
 *   input whatspeed = steps/second
 *   output step_delay = usec/step
 *   
 *   
 */
void ArdumotoStepper::setSpeed(unsigned short  whatSpeed)
{
    this -> step_delay = 1L * 1000L * 1000L / whatSpeed;
    //this->step_delay = 60L * 1000L * 1000L / (this->number_of_steps * whatSpeed);
    //While previous was correct this approach makes more logical sense  
}

/*  
*   report motor Step speed based on current step delay
*   output motorStepSpeed = steps/second
*/
short ArdumotoStepper::getStepSpeed()
{ //return speed in steps/second
  short motorStepSpeed;
  motorStepSpeed = 1000000/this->step_delay;
  return (motorStepSpeed);
}

/*
 * Sets the stepping mode
 */
void ArdumotoStepper::setStepMode(unsigned short mode)
{
  if (stepmode != mode)  // do not change if active mode is already same as commanded mode
  {
     this->stepmode = mode;

    if (mode == FULLSTEP)
    {
        //this->number_of_steps = 4;    ///2
        step_number = step_number/2;   // need to get sequence close to equivalent step if mode changes
    }
    else
    {
        //this->number_of_steps = 8;    //number of steps per full  doubles for half steps *2
        step_number = step_number*2;          // need to get sequence close to equivalent step if mode changes     
    }
  }
}

/*
 * Gets the stepping mode
 */
int ArdumotoStepper::getStepMode(void)
{
    return this->stepmode;
}

/*
 * release stepper (turn off power)
 */
void ArdumotoStepper::release(void)
{
    analogWrite(motor_pin_1, 0);
    analogWrite(motor_pin_2, 0);
}

/*
 * Moves the motor steps_to_move steps.  If the number is negative,
 * the motor moves in the reverse direction.
 */
void ArdumotoStepper::step(int steps_to_move)
{
    int steps_left = abs(steps_to_move);  // how many steps to take

    // determine direction based on whether steps_to_mode is + or -:
    if (steps_to_move > 0) { this->direction = 1; }
    if (steps_to_move < 0) { this->direction = 0; }

    // decrement the number of steps, moving one step each time:
    while (steps_left > 0)
    {
        unsigned long now = micros();
        // move only if the appropriate delay has passed:
        if (now - this->last_step_time >= this->step_delay)
        {
            // get the timeStamp of when you stepped:
            this->last_step_time = now;
            // increment or decrement the step number,
            // depending on direction:
            if (this->direction == 1)
            {
                this->step_number++;
                if (this->step_number == this->number_of_steps) {
                    this->step_number = 0;
                }
            }
            else
            {
                if (this->step_number == 0) {
                    this->step_number = this->number_of_steps;
                }
                this->step_number--;
            }
            
            // decrement the steps left:
            steps_left--;
            if (this->stepmode == FULLSTEP)
                stepMotor(this->step_number % 4);
            else
               halfstepMotor(this->step_number % 8);
        }
    }
}
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

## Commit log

2021-01-16 Bug fixes and operation enhancement Signed-off-by: benkot <benkotodd@gmail.com> Version 2.0.1 Bug fixes to firmware and modify firmware operation - fix motor stoppage after 30second run because of te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
    [ArdumotoStepper.cpp]
2021-01-16 Bug Fix to speed change - for position changes < 250 steps, unit would start with speed set to number steps in the position change per second. This would extend all way up to 250 steps /second. - Uni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
    [PnPFocus-V2.0.ino]
